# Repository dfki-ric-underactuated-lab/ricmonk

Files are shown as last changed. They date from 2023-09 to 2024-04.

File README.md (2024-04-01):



<div align="center">

# RicMonk: A Three-Link Brachiation Robot with Passive Grippers

</div>

<div align="center">

</div>

## Description
This project offers an open-source and low-cost kit to test control algorithms for underactuated robots. 
It introduces a three-link underactuated brachiation robot called **RicMonk** capable of bidirectional brachiation maneuver with passive grippers inspired from [AcroMonk](https://github.com/dfki-ric-underactuated-lab/acromonk).
RicMonk has two Quasi-Direct-Drives (QDD) that allow dynamic and agile locomotion. 
This project offers different control methods for trajectory stabilization which can be studied using the kit. Additionally, it provides a list of components, discusses best practices for implementation, and presents results from experiments with the simulator and the real system. This repository describes the hardware (CAD, Bill Of Materials ([BOM](/hardware/bills-of-materials.md)), etc.) required to build the physical system and provides the software (URDF models, simulation, and controllers) to control it.

## Research Paper

The work is submitted to the IEEE International Conference on Robotics and Automation (ICRA 2024) and is currently under review. 

## Documentation

The following provides theoretical information regarding the RicMonk:
- [Mechatronic design and integration](/hardware/mechDesAndInt.md)
- [Trajectory optimization](/software/python/simulation/behavior_generation/trajectory_optimization/README.md)
- [Trajectory stabilization](/software/python/simulation/behavior_control/README.md)
- [Bill Of Materials BOM](/hardware/bills-of-materials.md)

For operating the RicMonk, the following may serve as a reference:
- [Basic information](/hardware/README.md)
- [Brachiaiton realization](/software/python/realSystemTests/multipleBrachiationRealize.md)
- [Software Guide](/software/python/README.md)

The CAD file is also provided on grabCAD.com. You can use the 3D viewer from their website to display the 3D model directly within your browser.
 - [Display RicMonk in 3D](https://grabcad.com/library/ricmonk-a-three-link-underactuated-brachiation-robot-with-passive-grippers-1)
## Authors #

* [Shivesh Kumar](https://robotik.dfki-bremen.de/en/about-us/staff/person/shku02) (Team Leader - Mechanics and Control)
* [Mahdi Javadi](https://robotik.dfki-bremen.de/en/about-us/staff/person/maja04) (Project Supervisor, Hardware and Software Concepts, Trajectory Optimization and Stabilization)
* Shourie S. Grama (Hardware and Software Maintainer, Design Optimization, Trajectory Optimization and Stabilization)
* [Hossein Zamani Boroujeni](https://robotik.dfki-bremen.de/en/about-us/staff/person/hoza01) (Tail Design and Gripper Design Improvement. The credit for original arm and gripper design goes to [Daniel Pizzutilo](https://robotik.dfki-bremen.de/de/ueber-uns/mitarbeiter/dapi01) in [AcroMonk](https://github.com/dfki-ric-underactuated-lab/acromonk))

Feel free to contact us if you have questions about the test bench. Enjoy!

## Contributing

1. Fork it (<https://github.com/yourname/yourproject/fork>)
2. Create your feature branch (`git checkout -b feature/fooBar`)
3. Commit your changes (`git commit -am 'Add some fooBar'`)
4. Push to the branch (`git push origin feature/fooBar`)
5. Create a new Pull Request

## Safety Notes #

When working with a real system be careful and mind the following safety measures:

* Brushless motors can be very powerful, moving with tremendous force and speed. Always limit the range of motion, power, force, and speed using configurable parameters, currently limited supplies, and mechanical design.

* The robot must be placed in a ladder bar cage and kept at least one distance from the acromonk in case of operation.

* Make sure you have access to an emergency stop while doing experiments. Be extra careful while operating in the pure torque control loop.

* The robot is equipped with an onboard Lithium Polymer battery and needs proper care and attention. Make sure that you have all the necessary information for the LiPo batteries.

## Acknowledgments #
This work has been supported by the M-RoCK (FKZ01IW21002) and VeryHuman (FKZ01IW20004) projects funded by the German Aerospace Center (DLR) with federal funds from the Federal Ministry of Education and Research (BMBF) and is additionally supported with project funds from the federal state of Bremen for setting up the Underactuated Robotics Lab (201-342-04-2/2021-4-1).

<div align="center">

</div>

## License

This work has been released under the BSD 3-Clause License. Details and terms of use are specified in the LICENSE file within this repository. Note that we do not publish third-party software, hence software packages from other developers are released under their very own terms and conditions, e.g. Stable Baselines (MIT License) and Tensorflow (Apache License v2.0). If you install third-party software packages along with this repo ensure that you follow each license agreement.

## Citation

1. Grama S., Javadi M., Kumar S., Zamani H., Kirchner F., (2024). RicMonk: A Three-Link Brachiation Robot with Passive Grippers for Energy-efficient Brachiation. Submitted in: IEEE International Conference on Robotics and Automation (ICRA).
```
@article{2024_ICRA_ricmonk,
  title={RicMonk: A Three-Link Brachiation Robot with Passive Grippers for Energy-efficient Brachiation},
  author={Grama, Shourie S and Javadi, Mahdi and Kumar, Shivesh and Zamani Boroujeni, Hossein and Kirchner, Frank},
  note={Accepted January 29, 2024 in International Conference on Robotics and Automation (ICRA)}}
```

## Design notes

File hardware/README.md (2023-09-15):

# RicMonk: basic information

Mechatronic design and integration of the RicMonk is addressed [here](../hardware/mechDesAndInt.md). 

## Raspberry Pi and its setup instructions
Raspberry Pi4([setup instructions](https://projects.raspberrypi.org/en/projects/raspberry-pi-setting-up)) is used as a proccessing unit for the RicMonk. Since the Raspberry Pi is housed in the RicMonk, communication to the Raspberry Pi is executed over WiFi using a server computer. An SSH connection is established over WiFi between the server and the Raspberry Pi. To do so, the following steps may be utilized:
- Setup a router
- Connect the Raspberry Pi to a keyboard, a mouse, and a monitor and then power it up
- Connect the Raspberry Pi to the router via WiFi
- Connect the server computer to the router via WiFi
- Get the IP address of the Raspberry Pi using the command `hostname -I` on the Raspberry Pi command line
-Enable SSH/VNC by using `sudo raspi-config` in the Raspberry Pi command line
- Given the username of the Raspberry Pi is `pi` and the IP address is `ipaddress` use the command `ssh pi@ipaddress` the command line of the server

Once all this is set up, there is no requirement to connect the Raspberry Pi to the peripherals anymore. It can be used via SSH.

Information required for pi3hat configuration and commanding motors using tview has been detailed below.

# Moteus tools and Raspberry Pi

Welcome to the documentation for the Pi3hat and Raspberry Pi (RPi) integration. This guide is organized into the following sections:

- Installation
- Sending Commands Using `tview`
- Useful Terminal Commands
- IMU Sensor Data Readings

## Installation

To get started, you'll need to install the necessary dependencies. Follow these steps:

1. Install `moteus` and `moteus_pi3hat` by running the following commands:

```bash
pip3 install moteus
sudo apt install python3-pyside2* python3-serial python3-can python3-matplotlib python3-qtconsole
sudo pip3 install asyncqt importlib_metadata pyelftools
sudo pip3 install --no-deps moteus moteus_gui
sudo pip3 install moteus_pi3hat
```

If you encounter issues related to the `PySide2` dependency, execute these commands:

```bash
pip install PySide2
pip3 install PySide2
sudo apt install python3-pyside2* python3-serial python3-can python3-matplotlib python3-qtconsole
```

Afterward, try installing `moteus_pi3hat` again:

```bash
sudo pip3 install moteus_pi3hat
```

## Sending Commands Using `tview`

Depending on your specific configuration, which includes the bus connected (e.g., CAN) and motor ID, you can use the `tview` tool to connect to your motors. Execute the following command, replacing `BUS` and `MOTOR_ID` with your actual values:

```bash
sudo python3 -m moteus_gui.tview --pi3hat-cfg 'BUS=MOTOR_ID' -t MOTOR_ID
```

For instance, if your CAN connector is attached to `JC3` and the motor ID is `1`, use the following command:

```bash
sudo python3 -m moteus_gui.tview --pi3hat-cfg '3=1' -t 1
```

## Useful Terminal Commands

You can control and manage your motors using terminal commands. To stop or zero-offset a motor, execute these commands, ensuring you adjust the `--pi3hat-cfg` and `-t` options according to your setup. For example, if your CAN connector is connected to `JC3` and the motor ID is `1`, use the following commands:

- Zero-offset the motor:

```bash
sudo moteus_tool --zero-offset --pi3hat-cfg '3=1' -t 1
```

- Stop the motor:

```bash
sudo moteus_tool --stop --pi3hat-cfg '3=1' -t 1
```

### Important Note for Motor and Pi3hat Configuration

Please note that the motor ID for the system is currently set to `7`. Additionally, the only compatible buses with the Pi3hat are `J3` and `J5`. To connect to the motor with the current configuration, use one of the following commands:

```bash
sudo python3 -m moteus_gui.tview --pi3hat-cfg '3=7' -t 7
```

or

```bash
sudo python3 -m moteus_gui.tview --pi3hat-cfg '5=7' -t 7
```

## IMU Sensor Data Readings

### Reading IMU Data from Terminal

To access IMU data, you will need the `pi3hat_tools`. You can download a precompiled version of `pi3hat_tools` by following [this link](https://github.com/mjbots/pi3hat/releases/download/0.1-20210609/20210609-pi3hat_tools-d1e8aa529fe9aa62e6c0df19f10b83bd0e743273.tar.bz2).

**Note:** If your Raspberry Pi does not have an internet connection, you can download the file on your laptop and transfer it to the Raspberry Pi using the steps outlined [here](https://spellfoundry.com/docs/copying-files-to-and-from-raspberry-pi-and-mac/).

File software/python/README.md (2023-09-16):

<div align="center">

# Software guide
</div>

This document provides instruction guides on executions of the software package in simulation and on the Raspberry Pi for real-time execution.

- [Simulation guide](simulation/README.md)
- [RicMonk system guide](realSystemTests/README.md)

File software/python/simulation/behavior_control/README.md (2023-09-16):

# Trajectory Stabilization

Trajectory stabilization is crucial for all robots to ensure trajectory tracking and it has been implemented in RicMonk to help the robot perform brachiation motion. Model-based [Time-varying Linear Quadratic Regulator (TVLQR)](/software/python/simulation/behavior_control/controllers/tvlqr/README.md) and model-free [Proportional-Integral-Derivative (PID) controller](/software/python/simulation/behavior_control/controllers/pid/README.md) that are employed to stabilize the optimal trajectories for the RicMonk.

## Operation
 The file **trajStabilization.py** is to run for stabilizing the trajectories recently optimized, i.e. the trajectories that would be in the folder named after the maneuver in [here](/data/trajectories/direct_collocation/), according to the maneuver. Input the maneuver to be stabilized and also the type of controller to be used (PID or TVLQR). The gains, for either of the controllers have been tuned to enable the controllers to track the trajectories that are stored. The gains may also be modified according to the user's choice by opening the Python file. Running the file would generate the stabilized trajectories. These stabilized trajectories are stored in the folder named concerning the maneuver, controller type, and the date and time of the program run in [here](/data/simulation/). Additionally, the .csv file with the trajectory data and the gains used to stabilize the respective trajectory are also saved in [here](/data/trajectories/closed_loop).

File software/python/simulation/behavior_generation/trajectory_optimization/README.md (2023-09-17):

<div align="center">

# RicMonk Trajectory Optimization
</div>

## Fixed-base model
To optimize trajectories for brachiation, simplify the system, and improve the probability of finding optimal solutions, we use a fixed-base model of the robot as shown in the following figure.

<div align="center">
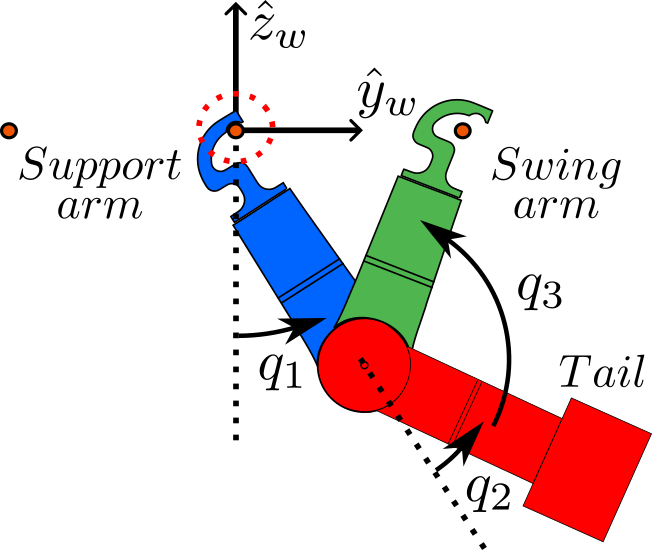
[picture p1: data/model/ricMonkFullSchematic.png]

</div>

In such a model for the RicMonk, the joint between $arm_1$ and ladder bar at $\mathbf{(y_{c}, z_{c})}$ is a revolute joint(dotted circle in the figure). In reality, the arm in contact with the support bar can move if enough force is applied to the arm. Making use of such a model reduces the number of constraints to be imposed, hence simplifying the problem. However, the use of such a fixed-base model has its disadvantages. $arm_1$ cannot let go of the bar, hence trajectories where that happens may not be optimized using this model.

The study on [AcroMonk](https://github.com/dfki-ric-underactuated-lab/acromonk), a two-linked brachiation robot, that is capable of continuously performing robust multiple brachiation maneuvers describes the use of a state machine. The state machine is an implementation that helps the robot to continually brachiate either forward or backward while taking the failure of brachiation into account. For instance, when the robot is not able to successfully catch the bar, when the robot loses all contact with the bar and falls on the ground, when the arm slips off the ladder bar, etc. Given a situation with the robot in any of these cases, the robot either tries to brachiate again using some recovery trajectories or shuts down the actuators to keep the user, the environment, and the robot itself safe. To have such an efficient state machine, the complex brachiation motion was broken down into four distinct simpler maneuvers(a.k.a. atomic behaviors), **ZB**, **ZF**, **BF**, and **FB**. These maneuvers translate respectively to 'zero to back', 'zero to front', 'back to front', and 'front to back'. The forward direction of motion is considered to be the direction in which the hook forms a concave shape. Each of these trajectories is illustrated in the following section. Such an implementation of a state machine enables the robot to perform continuous robust brachiation, even in the face of disturbances. In addition, it simplifies the task of optimizing trajectories. 

Formulation of the trajectory optimization problem is described in [here](formulation.md)

## Gripper Heuristics
Grasp constitutes the action of the robot swing arm hooking onto the surface of the ladder bar, whereas release constitutes the action of the robot swing arm letting go of the ladder bar. Trajectory optimization as [formulated](formulation.md) does not include grasp and release actions, as it does not consider the contact dynamics of the system. As a result, trajectories are optimized from the time instant after the swing arm would have performed the release action to the moment before the swing arm performs the grasp action. These trajectories are called atomic behaviors. Generally, the actions of the swing arm performing release and grasp require the application of a feed-forward torque to the robot's motors. In the case of RicMonk, the weight of the robot and the velocity of the approach of the swing arm toward the target ladder bar take care of the grasp. Hence, for RicMonk to perform the grasp action, no feed-forward torque is applied. However, to perform the release and grasp actions, direct feed-forward torque is applied to the actuators in appropriate directions. The directions and magnitude of the torques were calculated empirically. The following image describes the directions of force applied on the arms due to torque generated in respective motors to enable the robot to perform a release action.

<div align="center">
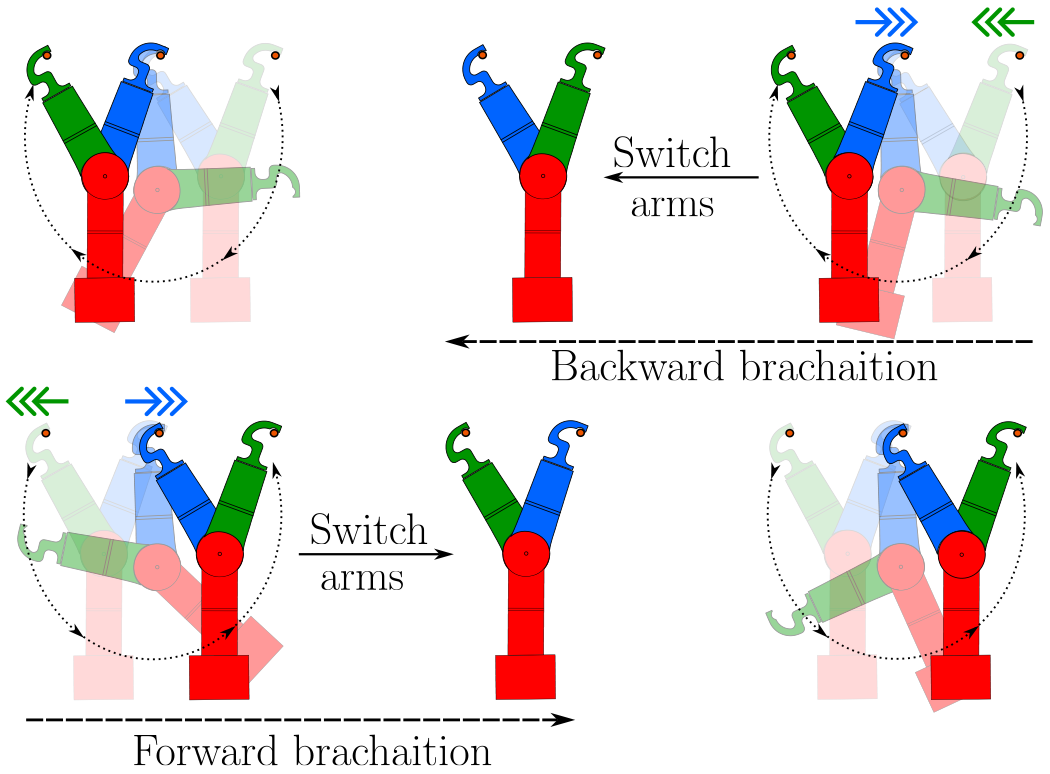
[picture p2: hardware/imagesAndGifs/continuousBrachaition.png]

</div>

To validate the release of the grasp, we monitor the velocity of the swing arm. When the swing arm is still grasping the ladder bar, its velocity remains minimal. We have set a threshold velocity of 1.2 rad/s, which indicates a successful release when the swing arm reaches this velocity. Our tests ensure that only minimal torque is applied to release the grasp from the ladder bar.

## Atomic Behaviors
The swing trajectories for these atomic behaviors are optimized and the animations are obtained as follows. 

<!-- <div align="center">
<img width="500" src="data/model/stateMachine.png" />
</div> -->

<div align="center">
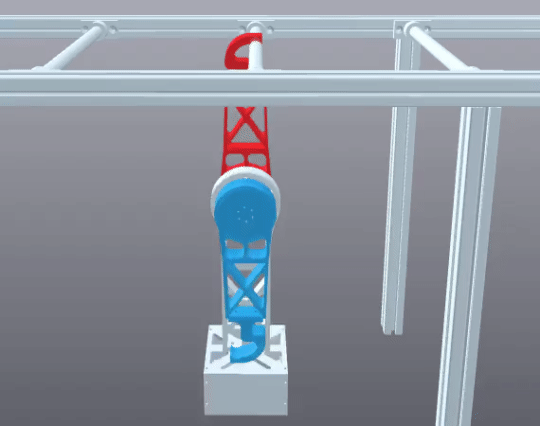
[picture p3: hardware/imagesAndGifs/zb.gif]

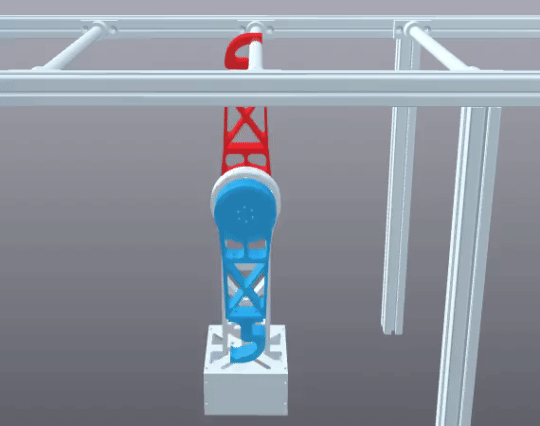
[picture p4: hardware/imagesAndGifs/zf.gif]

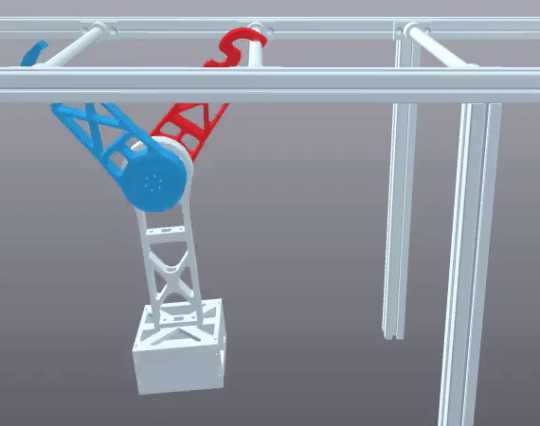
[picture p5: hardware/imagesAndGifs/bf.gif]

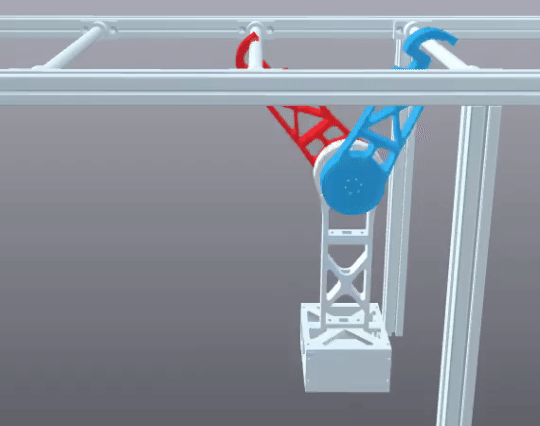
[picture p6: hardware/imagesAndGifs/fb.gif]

</div>

<!---
<div align="center">
<img width="200" src="hardware/imagesAndGifs/ZB_ini_gif.gif" >
<img width="200" src="hardware/imagesAndGifs/ZF_ini_gif.gif" >
<img width="200" src="hardware/imagesAndGifs/BF_ini_gif.gif" >
<img width="200" src="hardware/imagesAndGifs/FB_ini_gif.gif" >
</div>
-->

## Operation
The folder **direct_collocation** contains files that provide the respective hyper-parameters for optimizing trajectories. The file **simulateTrajOpt.py** is to run for optimizing trajectories. Input the name of the trajectory (ZB, ZF, BF, FB) and the ladder bar distance (default = 0.34m). The optimized trajectories are saved in the folder with the name of the maneuver in [here](/data/trajectories/direct_collocation/), according to the maneuver.

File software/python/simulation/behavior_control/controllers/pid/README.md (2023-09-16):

#  Proportional–Integral–Derivative (PID) Control 

## Theory 

The Proportional-Integral-Derivative(PID) controller is a model-free controller, that generates the amount of torque($\mathbf{u}$) supplied by the motors to compensate for the error in the generalized positions($\mathbf{q}$) and velocities($\dot{\mathbf{q}}$) of the robot. The gains $K_p$, $K_i$, and $K_d$ are the proportional, integral, and derivative gains that control the impact of error compensation in generalized positions and velocities respectively. If the desired position and velocity vectors are represented by $\mathbf{q}^*$ and $\dot{\mathbf{q}}^*$, the following equation presents the governing equation of the PID controller.

```math
\begin{equation*}
    \mathbf{u}(t) = K_p \cdot (\mathbf{q}^*(t) - \mathbf{q}(t)) + K_i \cdot \int_{0}^{t} (\mathbf{q}^*(t) - \mathbf{q}(t)) dt + K_d \cdot (\dot{\mathbf{q}}^*(t) - \dot{\mathbf{q}}(t))
\end{equation*}
```

PID controllers are simple to implement. They are efficient in reducing steady errors and they improve system stability. However, the three gains that are required to be manually tuned may pose an error while tuning.  On the other hand, they do not require the model of the system, and their performance is not related to the accuracy of the mathematical model. They may be applied to various systems, and they deliver robust performances.

## Dependencies

The trajectory optimization using direct collocation and PID gains are obtained by taking advantage of [Drake toolbox [2]](https://drake.mit.edu/).

## References

[[1] Russ Tedrake. Underactuated Robotics: Algorithms for Walking, Running, Swimming, Flying, and Manipulation (Course Notes for MIT 6.832).](http://underactuated.mit.edu/)

[[2] Model-Based Design and Verification for Robotics](https://drake.mit.edu/).

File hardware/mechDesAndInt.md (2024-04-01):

<div align="center" >

# Mechatronic Design an Integration
</div>

## Mechanics
Mechanical Design Optimization and integration of necessary electrical components for a functional, capable, and safe operation of a robotic system constitute the Mechatronic integration of the robot. Inspired by the [AcroMonk](https://github.com/dfki-ric-underactuated-lab/acromonk), RicMonk was designed to portable and robust. RicMonk, guided by
the concept of interchangeable and reusable components, stands ready to adapt effortlessly to evolving circumstances. From the bio-inspiration perspective, the RicMonk is closer to Gibbons because of the presence of the tail when compared to the AcroMonk. RicMonk’s tail also plays an important role in the robot’s functioning. It not only provides optimal placement of all the electrical components but also helps extensively in helping the robot brachiate.

<div align="center">
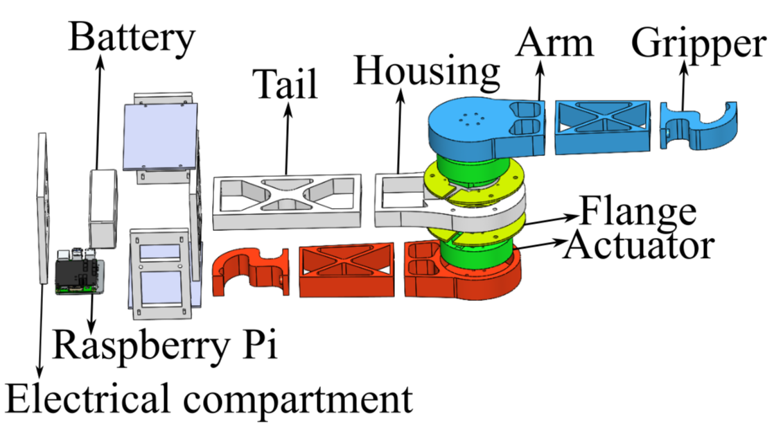
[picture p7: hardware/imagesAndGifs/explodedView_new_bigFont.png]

</div>

<div align="center">
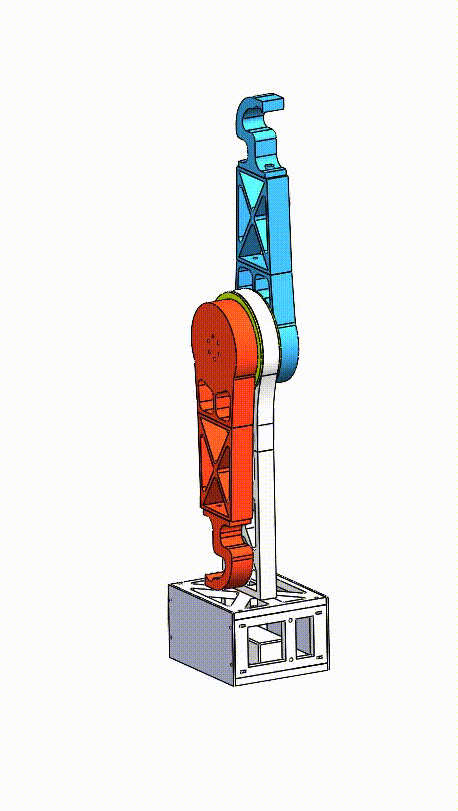
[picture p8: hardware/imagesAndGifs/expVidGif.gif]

</div>

## Electronics
The schematic of the electrical diagram is shown in the following figure.

<div align="center">
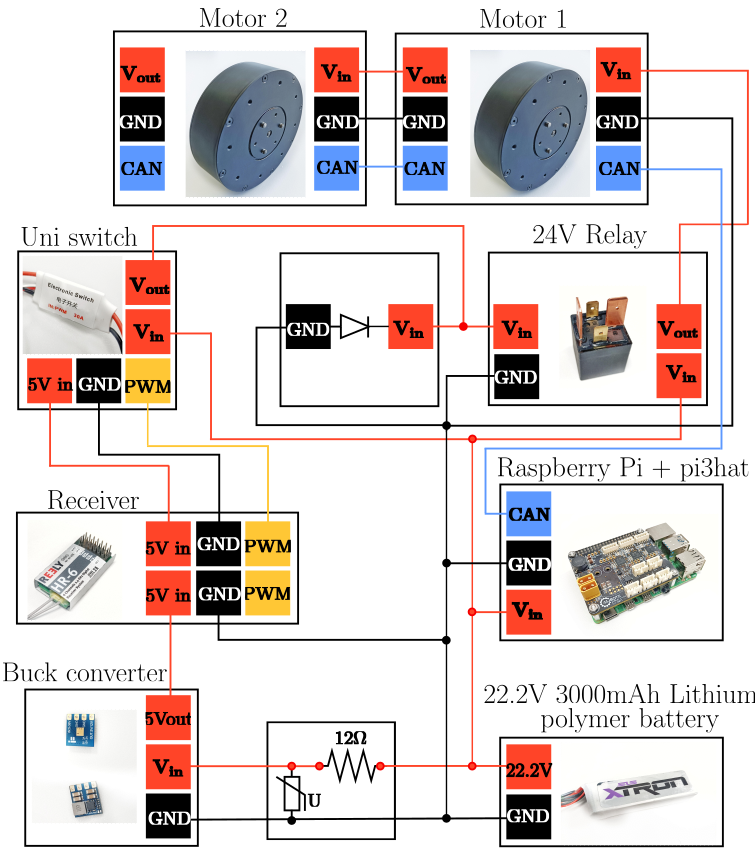
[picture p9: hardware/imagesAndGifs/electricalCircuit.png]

</div>

### Battery
All electronics of the AcroMonk are powered by a LiPo battery with the following technical data:
- Capacity: $6\text{S}\ 3000 \text{ mAh}$ 
- Voltage: $22.2\text{V}$
- Continuous Discharge: max. $30\text{C } (36\text{A})$
- Burst Discharge:max. $60\text{C } (72\text{A})$
- Power: $26.64 \text{ WH}$

### Raspberry Pi and pi3hat
A Raspberry Pi4B ([setup](/hardware/README.md) is used as a processing unit for the robot, and the [mjbots pi3hat](https://mjbots.com/products/mjbots-pi3hat-r4-4b) is used for communication between the Raspberry Pi and the motors. The Inertia Measurement Unit (IMU)([usage](https://github.com/mjbots/pi3hat/blob/master/lib/python/examples/imu_example.py)) on the pi3hat is also used for state estimation purposes. The Raspberry Pi is connected, via WiFi using a Secure Shell Protocol (SSH), to the server that is operated by the user. The Raspberry Pi stores the desired trajectories, the applications to run the robot and help it track trajectories, and measured trajectories.

### Actuator
The actuators used in the RicMonk are the mjbots [qdd100](https://mjbots.com/collections/servos-and-controllers/products/qdd100-beta-3) actuators. These motors are quasi-direct drive motors that provide high torque with sufficient power. These motors also provide the advantages of being back-drivable. 
- [Documentation](https://github.com/mjbots/moteus)
- [Setup](https://www.youtube.com/watch?v=HHCBohdrCH8)

### Emergency Stop
It is necessary to have a safety switch to switch OFF the motors when the robot has an undesired erratic behaviour. To implement the safety switch, a Radio Communication Transmitter Protocol (TX protocol) has been employed to enable a safe operation of the robot. As a result, the electrical circuit includes a transmitter and a receiver. The wiring between the receiver connects to the motors via a 25 A relay, a diode and a 30 A electrical switch. To lower the voltage to the receiver (rated voltage: 6.5 V), a DC-DC converter is used. To avoid the DC-DC converter from getting burnt due to the high frequency voltage fluctuations when the circuit is switched ON, a series combination of a Varistor and a resistor is added to the circuit. This addition dampens the voltage fluctuations in the circuit. As
a result, based on the command from the transmitter, the motors can be directly switched ON and OFF. The electrical switch only controls the functioning of the motors, so the computer (Raspberry Pi) is unaffected by the switching ON and OFF of the motors.

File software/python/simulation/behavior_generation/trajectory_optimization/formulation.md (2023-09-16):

# Trajectory optimization formulation
Taking advantage of the Direct Collocation method by the [Drake](https://drake.mit.edu/) toolbox, and the fixed-base model of the robot, trajectories are optimized for the swing phases using the Sparse Nonlinear OPTimizer([SNOPT](https://www.jstor.org/stable/20453604)). The optimization problem is formulated as follows:

```math
\begin{align*}
    \text{Minimize } \quad & J = W(t_f) + \sum_{n=0}^{N} R(T_1(u_1[n])^2 + T_2(u_2[n])^2) + K(V_1(q_2[n])^2 + V_2(q_3[n])^2) \\
    \text{s.t. } \quad & \text{Dynamics: } \dot{\mathbf{x}}(t_n) = f(\mathbf{x}(t_n), \mathbf{u}(t_n)) \\
    & \text{Costate dynamics: } \dot{\lambda}(t) = -\frac{\partial H}{\partial \mathbf{x}} \\
    & \text{Hamiltonian: } H = L(\mathbf{x}(t_n), \mathbf{u}(t_n)) + \lambda^T f(\mathbf{x}(t_n), \mathbf{u}(t_n)) \\
    & \text{Boundary conditions: } \begin{aligned}[t] 
        \mathbf{x}[0] &= \mathbf{x}_0, \\
        \mathbf{x}[t_f] & \text{ defined using forward geometry and kinematics} \\
        \end{aligned}\\
    & \text{Time step constraint: } 0.005 \leq h[n] \leq 0.5 \\
    & \text{Torque constraints: } |\mathbf{u}[n]| \leq \tau_{\max} \\
    & \text{Velocity constraints: } |\dot{q}_1[n]|, |\dot{q}_2[n]|, |\dot{q}_3[n]| \leq \omega_{\max} \\
    & \text{Position constraints: } |q_1[n]| \leq q_{lim, 1}, |q_2[n]| \leq q_{lim, 2}, |q_3[n]| \leq q_{lim, 3} \\
    & \text{Collision constraints defined using forward geometry}\\
    & \text{Optimization problem warm-started using previously generated trajectories}
\end{align*} 
```
```math
\begin{equation*}
    \mathbf{x} = \begin{bmatrix}
        q_1 \\ q_2 \\ q_3 \\ \dot{q_1} \\ \dot{q_2} \\ \dot{q_3}
    \end{bmatrix} = \begin{bmatrix}
        \mathbf{q} \\ \dot{\mathbf{q}}
    \end{bmatrix}
\end{equation*}
```
```math
\begin{equation*}
    \mathbf{u} = \begin{bmatrix}
        u_1 \\ u_2
    \end{bmatrix}
\end{equation*}   
```

$\mathbf{x}$ and $\mathbf{u}$ are the state vector and the torque vector respectively, and they are the decision variables of the current trajectory optimization problem. $N$ is the number of collocation points that consist of the trajectory. $\mathbf{h}$ is a vector that contains the timesteps that separate the collocation points. $\tau_{max}$ is the imposed motor torque limit and $\omega_{max}$ is the imposed motor angular velocity limit for safe operation of the robot. $q_{lim, 1}$, $q_{lim, 2}$, $q_{lim, 3}$ are the position limits for each of the joint angles. In the cost equation, $R$, $T_1$, and $T_2$ input regularization term and weighting factors for each of the actuators respectively. Also in the same equation, $K$, $V_1$, and $V_2$ are velocity regularization terms and weighting factors for each of the actuators respectively. $W$ is the time penalization constant. The boundary condition for the final time is defined using the forward geometry and kinematics, such that the free end of $arm_2$ catches is at the required position with the required velocity. From the model, we see that the connection of the tail to the arms leads to a kinematic coupling that is not purely serial. Consequently, the inverse kinematics alone cannot directly yield the robot's final state, denoted as $\mathbf{x}(t_f)$, which is a crucial requirement for trajectory optimization.

The output of the following code is not optimal. $\bf{Check}$!

To determine $\mathbf{x}(t_f)$, a methodology is employed involving the desired final spatial position and velocity of the swing arm's gripper, denoted as ${\bf{c}}^*_f$. In each iteration, the solver computes the system's forward kinematics based on the decision variable of the state, represented as $\mathbf{c}_{f}$, and strives to minimize the error relative to $\mathbf{c}_{f}^{*}$. Hence, the final position and velocity of the $tail$ are not explicitly constrained. Collision constraints concerning the free ends of the $tail$ and the $arm_2$ are also defined using the forward geometry of the robot.

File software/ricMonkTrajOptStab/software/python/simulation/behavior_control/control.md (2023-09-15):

# Trajectory Stabilization

Trajectory stabilization is crucial for all robots to ensure trajectory tracking and it has been implemented in RicMonk to help the robot perform brachiation motion. Model-based [Time-varying Linear Quadratic Regulator(TVLQR)](/src/ricMonkTrajOptStab/software/python/simulation/behavior_control/controllers/tvlqr/README.md) and model-free [Proportional-Integral-Derivative(PID) controller](/src/ricMonkTrajOptStab/software/python/simulation/behavior_control/controllers/pid/README.md) that are employed to stabilize the optimal trajectories for the RicMonk.
src="/"
## Operation
 The file **simulateTrajOpt_IPYNB.ipynb** is to run for stabilizing the trajectories recently optimized, i.e. the trajectories that would be in folder named after the maneuver in **../../../../../data/trajectories/direct_collocation/** with respect to the current folder. The **manuever** field may be modified to the choice of trajectory that needs to be optimized. Once done, run the file. The **controller_type** can also be changed to stabilized the trajectory using the PID controller or the TVLQR. The respective gains may be tuned using the variables provided.Running the file would generate the stabilized trajectories. These statbilized trajectories are stored in the folder named with respect to the maneuver, controller type and the date and time of program run. This folder is saved within the **../../../../../results** with respect to the current folder. Additionally, the .csv file with the trajectory data and the gains used to stabilize the respective trajectory are also saved in **../../../../../data/trajectories/closed_loop** with respect to the current folder.

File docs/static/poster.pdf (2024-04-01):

RicMonk: A Three-Link Brachiation Robot with Passive Grippers for Energy-Efficient Brachiation

Abstract
Brachiation (illustrated in Fig. 1), a mode common among primates like long-armed gibbons, involves swinging between tree branches using only their arms. This locomotion mode holds potential for diverse applications such as agriculture surveillance, forest exploration, and biomimetic design. This paper presents the design, analysis, and performance evaluation of RicMonk, a novel three-link brachiation robot equipped with passive hook-shaped grippers. The paper discusses the use of the Direct Collocation methodology for optimizing trajectories for the robot’s dynamic behaviors and stabilization of these trajectories using a Time-varying Linear Quadratic Regulator. With RicMonk we demonstrate bidirectional brachiation, and provide comparative analysis with its predecessor, AcroMonk [1]- a two-link brachiation robot, to demonstrate that the presence of a passive tail helps improve energy efficiency.

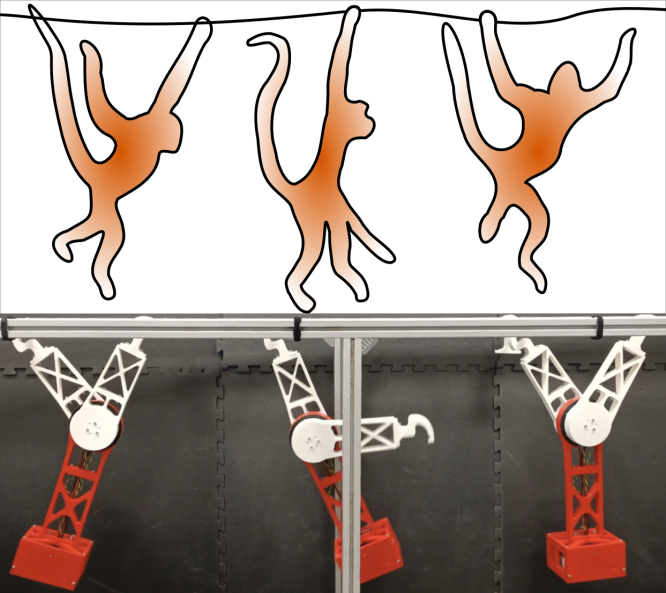
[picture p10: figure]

Figure: Brachiation illustration

Open-source code

The system design, controllers, and software implementation are publicly available on GitHub and the video demonstration of the experiments can be viewed on Youtube. Scan the following QR code to access the GitHub page where the link to the Youtube video is also available.

Mechatronics Design

As envisioned in the preceding generation of the RicMonk, the AcroMonk [1], the design should be compact, and wireless and needs to be made of readily available and lowcost materials. The arms and passive gripper are inspired by AcroMonk. RicMonk is equipped with two actuators and a tail that mimics a monkey’s body, as depicted in Fig. 2. Electrical components and the battery reside securely in the tail’s bottom box. A stable gripper design is critical during swinging. The original cylindrical pivot lacked stability due to an offset center of mass, causing sway and weak contact. This instability led to undesired motion with one arm on the ladder bar. To solve this, a conical pivotal surface was introduced, accommodating the offset. This improved stability, although a tight grip required higher release torque. Also, this gripper design results in mirroring symmetry rather than full sagittal symmetry in RicMonk.

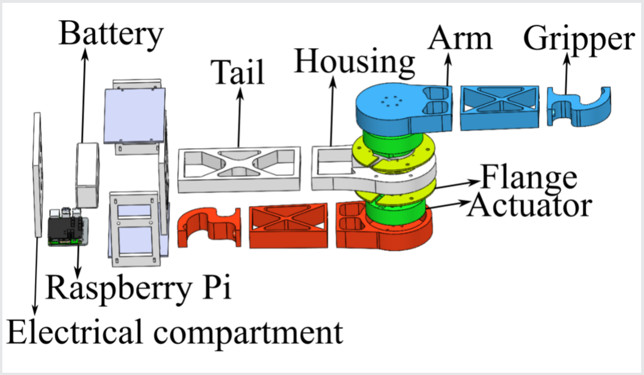
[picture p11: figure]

Figure: RicMonk exploded view

Trajectory Optimization

Brachiation is divided into four simple atomic behaviours -ZB (Zero - Back bar), ZF (Zero - Front bar), BF (Back bar
- Front bar), FB (Front bar - Back bar); as defined in [1]. These trajectories (state variables and inputs) are optimized, for a fixed base model of RicMonk (Fig. 3, dotted red circle represents a revolute joint), using the Direct Collocation method, by minimizing a cost dependent on the energy expended during the respective maneuver.

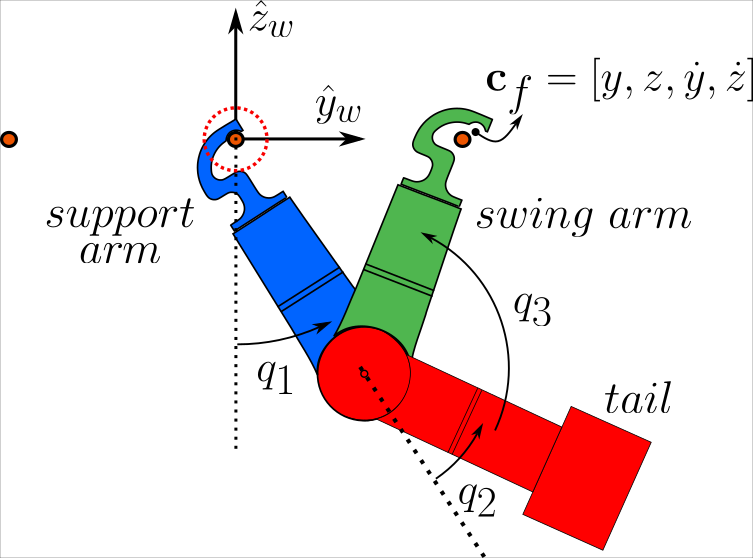
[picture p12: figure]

Figure: RicMonk fixed base model

Trajectory Stabilization

Each of the trajectories is stabilized using the Time-varying Linear Quadratic-Regulator (TVLQR) in simulation and reality. With the real system, TVLQR is used as an offline controller and the pre-computed optimal time-varying feedback matrix is used for online error compensation on a control loop running at approximately 400 Hz.

Experimental Validation

Atomic behaviors were executed on the real system using the TVLQR controller. State estimation accommodating the RicMonk arm’s complete revolution enabled combining atomic behaviors, facilitating continuous brachiation. Fig. 4 and 5 illustrate RicMonk performing multiple forward and backward directions respectively. The controller is robust against soft disturbances in the path of the robot, and excess weight. Fig. 6 displays variation in robot’s position during recovery from disturbance during brachiation.

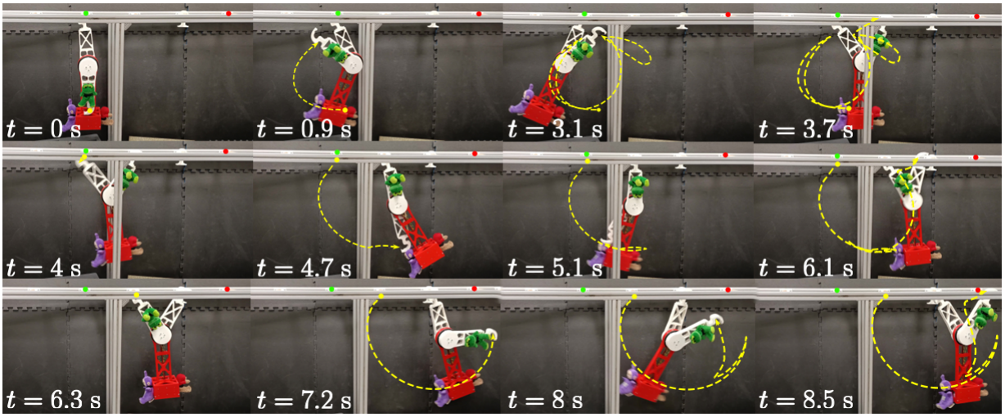
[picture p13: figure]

Figure: RicMonk performing multiple forward brachiation cycles. Row one - ZF maneuver (left to right), row two and three - BF maneuvers (left to right)

Comparative analysis

Cost of Transport (CoT) [2] is a dimensionless measure for energy efficiency, allowing comparison across sizes and structures. Formulated as Eq. 1, it factors in energy input (E), mass (m), distance (d), and gravity acceleration (g).

CoT =

E
mgd

(1)

The lower the CoT value, the more energy-efficient a given system is. Table 1 compares total energy consumed (TE), CoT, and time taken(t) during five continuous forward brachiation maneuvers for AcroMonk and RicMonk. RicMonk, with the tail, is more energy efficient compared to AcroMonk. However, AcroMonk consumes a lower amount of energy in total.

Table: Comparitive analysis
TE (J) CoT t (s)
AcroMonk 8.9547 0.3355 11
RicMonk 15.1947 0.2760 17

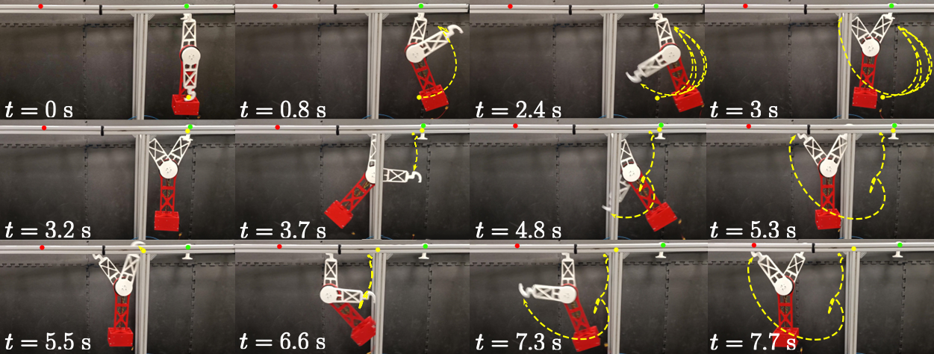
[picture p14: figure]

Figure: RicMonk performing multiple backward brachiation cycles. Row one - ZB maneuver (left to right), row two and three - FB maneuvers (left to right)

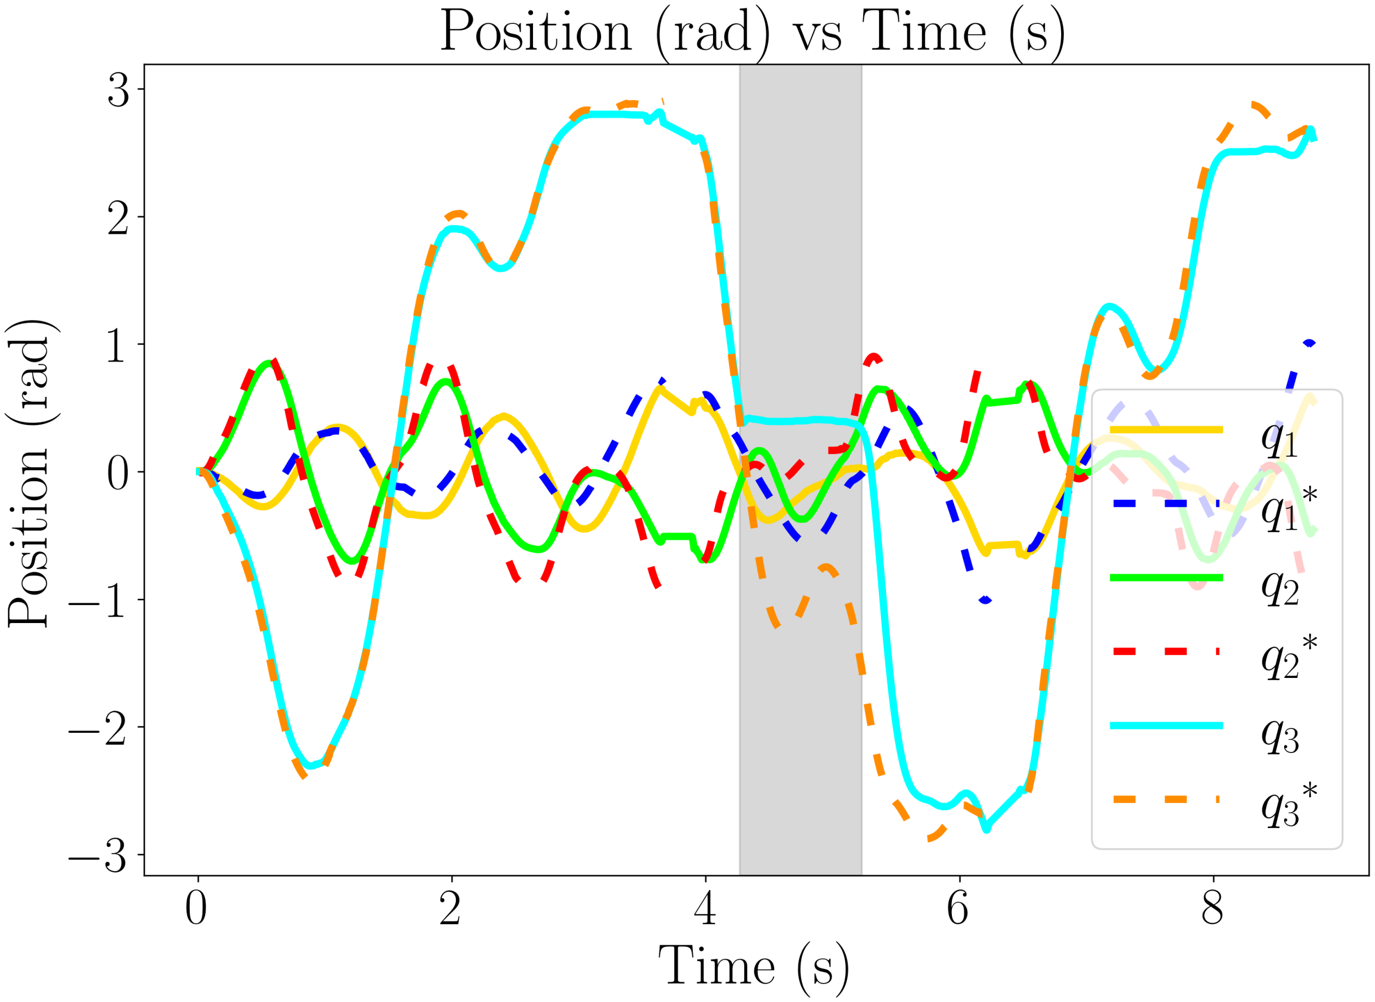
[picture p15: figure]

Figure: Position plot of RicMonk performing multiple brachiation in face of disturbances in its path. Shaded region of the plots signify disturbance in robot motion

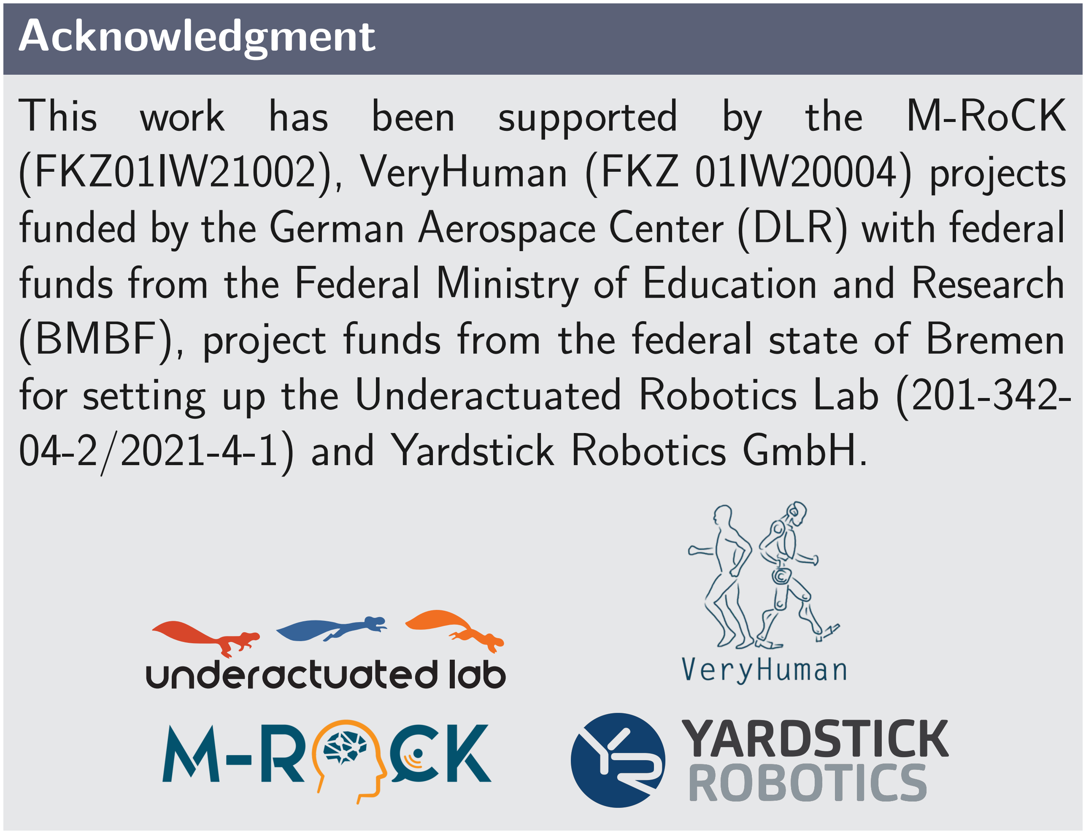
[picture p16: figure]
Acknowledgment; (FKZ01IW21002), VeryHuman (FKZ 01IW20004) projects; 04-2/2021-4-1) and Yardstick Robotics GmbH.

This work has been supported by the M-RoCK

funded by the German Aerospace Center (DLR) with federal funds from the Federal Ministry of Education and Research (BMBF), project funds from the federal state of Bremen for setting up the Underactuated Robotics Lab (201-342-

References

[1] Mahdi Javadi et al. “AcroMonk: A Minimalist Underactuated Brachiating Robot”. In: IEEE Robotics and Automation Letters (2023).
[2] Sangbae Kim, Patrick M Wensing, et al. “Design of dynamic legged robots”. In: Foundations and Trends® in Robotics 5.2 (2017), pp. 117–190.
Submission #1204 | shouriegs00.sgs@gmail.com, mahdi.javadi@dfki.de ,
1 Yardstick Robotics GmBH, Germany.

2 DFKI RIC GmbH, Germany.

3 University of Bremen, Germany.

4 Chalmers University of Technology, Sweden.

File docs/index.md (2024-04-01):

---
title: "RicMonk: A Three-Link Brachiation Robot with Passive Grippers for Energy-Efficient Brachiation"
pdf: https://arxiv.org/abs/2403.15762
youtube: https://youtu.be/hOuDQI7CD8w?si=d_ABz1Ux-a2fxKTy
github: https://github.com/dfki-ric-underactuated-lab/ricmonk
poster: static/poster.pdf
authors:
  - {name: Shourie S.  Grama, affiliation_key: 1, link: https://www.shouriegs.com/}
  - {name: Mahdi Javadi, affiliation_key: 1, link: https://robotik.dfki-bremen.de/de/ueber-uns/mitarbeiter/maja04.html}
  - {name: Shivesh Kumar, affiliation_key: [3,1], link: https://robotik.dfki-bremen.de/de/ueber-uns/mitarbeiter/shku02.html}  
  - {name: Hossein Zamani Boroujeni, affiliation_key: 1, link: https://robotik.dfki-bremen.de/de/ueber-uns/mitarbeiter/hoza01.html}
  - {name: Frank Kirchner, affiliation_key: [2,1], link: https://robotik.dfki-bremen.de/de/ueber-uns/mitarbeiter/frki01.html}
affiliations:
  - {name: German Research Center for Artificial Intelligence, affiliation_key: 1, link: https://robotik.dfki-bremen.de/de/startseite}
  - {name: Universität Bremen, affiliation_key: 2, link: https://www.uni-bremen.de/robotik}
  - {name: Chalmers University of Technology, affiliation_key: 3, link: https://www.chalmers.se/en/}

---

## Introduction
This paper presents the design, analysis, and performance evaluation of RicMonk, a novel three-link brachiation robot equipped with passive hook-shaped grippers. 
Brachiation, an agile and energy-efficient mode of locomotion observed in primates, has inspired the development of RicMonk to explore versatile locomotion and maneuvers on ladder-like structures. 
The robot's anatomical resemblance to gibbons and the integration of a tail mechanism for energy injection contribute to its unique capabilities. 
The paper discusses the use of the Direct Collocation methodology for optimizing trajectories for the robot's dynamic behaviors and stabilization of these trajectories using a Time-varying Linear Quadratic Regulator. 
With RicMonk we demonstrate bidirectional brachiation, and provide comparative analysis with its predecessor, [AcroMonk](https://github.com/dfki-ric-underactuated-lab/acromonk) - a two-link brachiation robot, to demonstrate that the presence of a passive tail helps improve energy efficiency. 
The system design, controllers, and software implementation are publicly available on [GitHub](https://github.com/dfki-ric-underactuated-lab/ricmonk).

## Experimental Results
Javadi *et al.* in [AcroMonk](https://arxiv.org/abs/2305.08373) proposed a state machine to ensure robust and continuous forward or backward brachiation while accounting for potential failures.  RicMonk also employs a similar state machine that integrates *gripper-related heuristics* with a swing phase to generate a maneuver. The swing motion is associated with a sequence of transitions among three fixed configurations, referred to as [*atomic behaviors*](https://github.com/dfki-ric-underactuated-lab/ricmonk/blob/main/software/python/simulation/behavior_generation/trajectory_optimization/README.md).

All the atomic behaviors are [tested with RicMonk](https://youtu.be/hOuDQI7CD8w?t=20) and only continuous backward brachiation is presented here for brevity. 

<figure>
  
  <figcaption>Fig.1 - RicMonk performing continuous backward brachiation</figcaption>
</figure>

## Results and Discussion

<table>
  <tbody>
    <tr align="center" valign="center">
      <td>
        <figure>
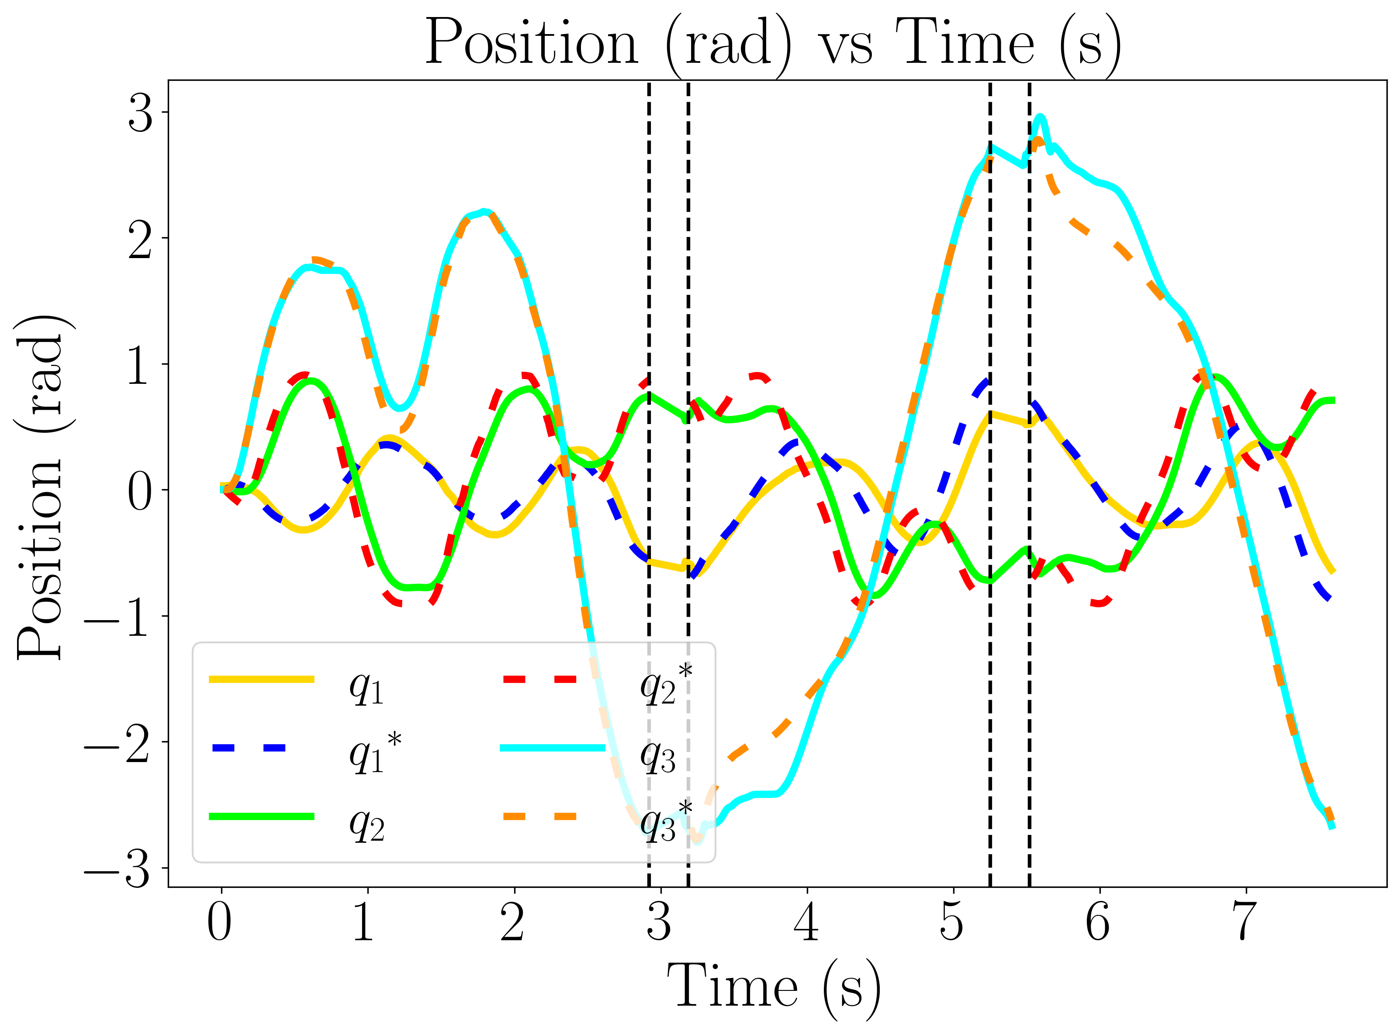
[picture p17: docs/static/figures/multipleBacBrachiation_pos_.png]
          
          <figcaption>Fig.2 - Position plot for backward brachiation</figcaption>
        <figure>
      </td>
      <td>
        </figure>
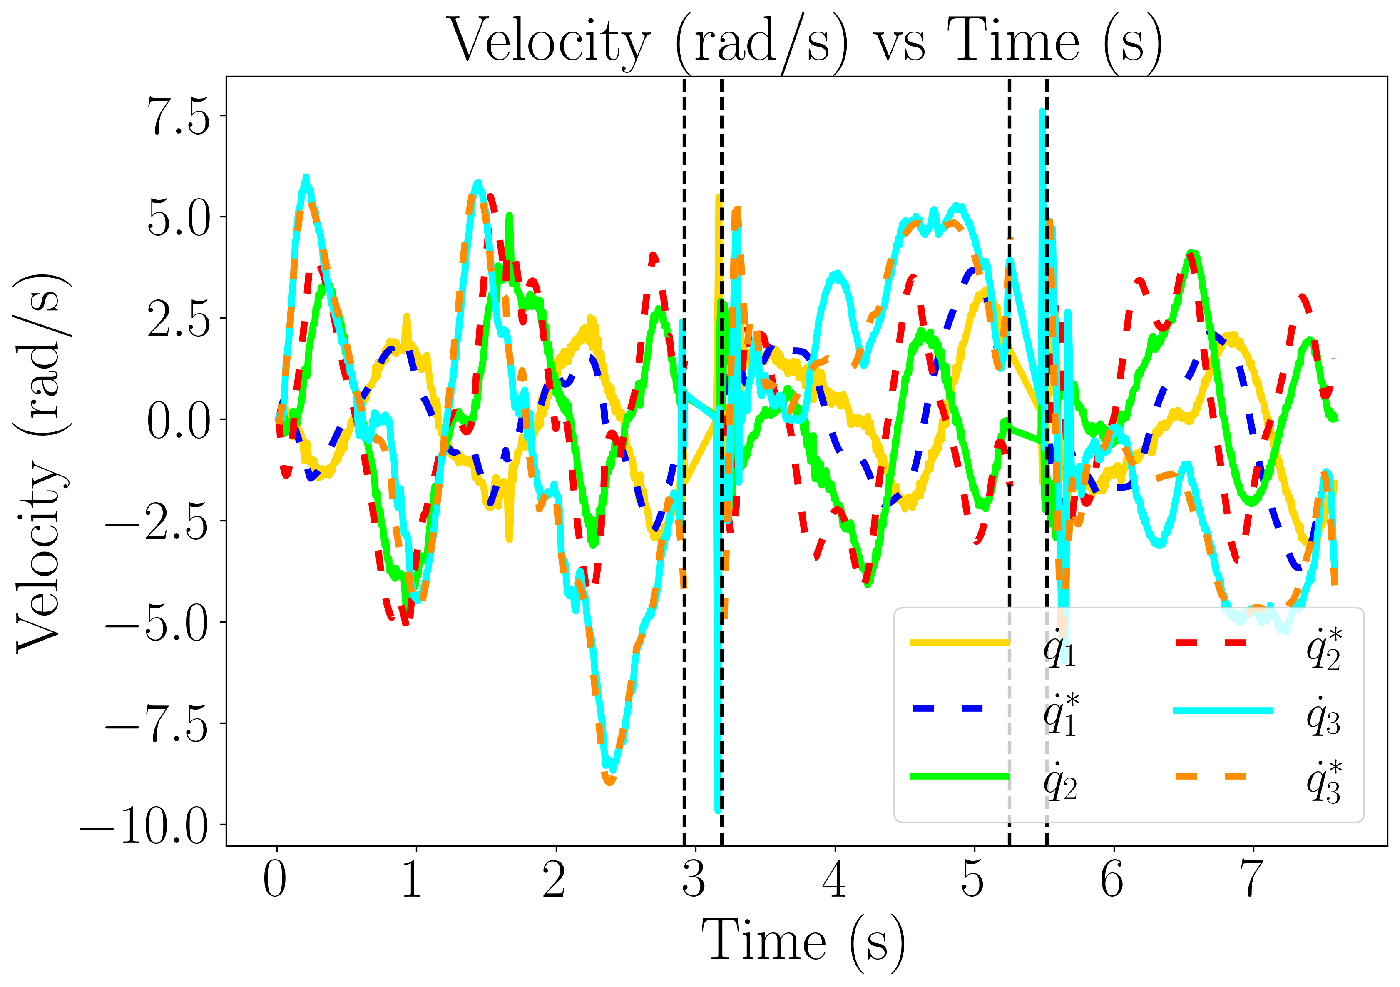
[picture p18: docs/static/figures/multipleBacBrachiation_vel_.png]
          
          <figcaption>Fig.3 - Velocity plot for backward brachiation</figcaption>
        </figure>
      </td>
    </tr>
    <tr align="center" valign="center">
      <td>
        <figure>
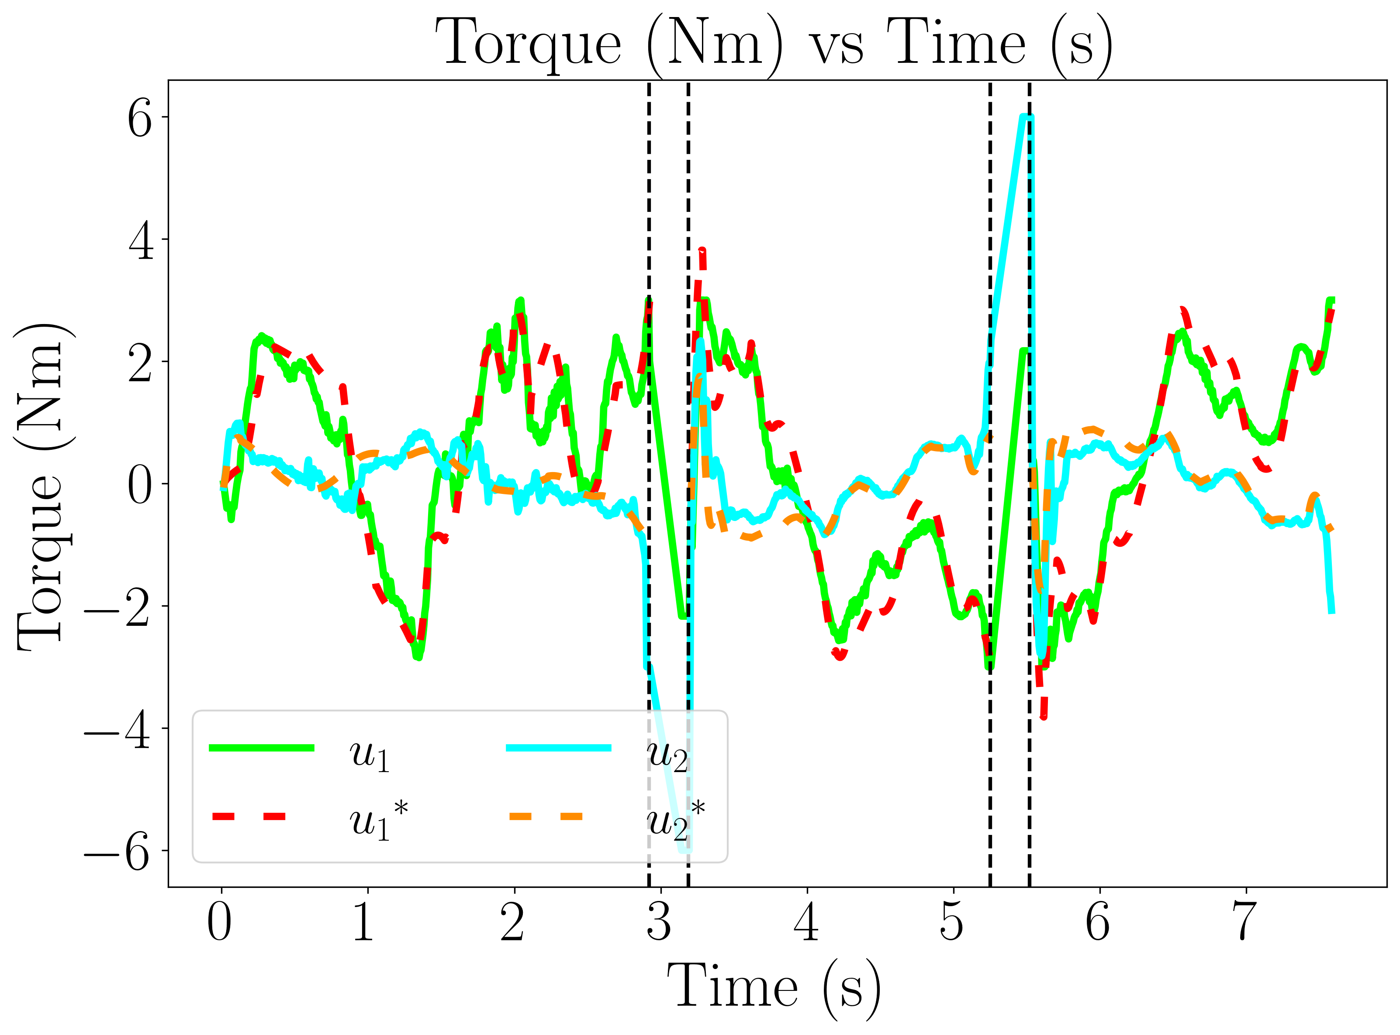
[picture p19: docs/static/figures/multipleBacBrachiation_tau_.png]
          
          <figcaption>Fig.4 - Torque plot for backward brachiation</figcaption>
        </figure>
      </td>
      <td>
        <figure>
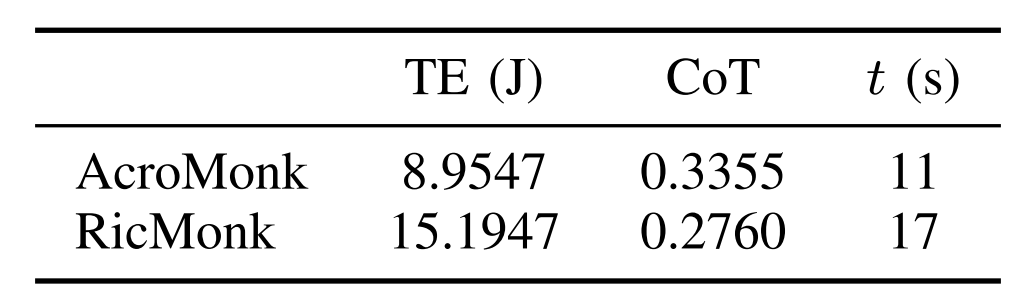
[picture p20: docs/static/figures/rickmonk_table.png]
          
          <figcaption>Table.1 - Comparitive analysis</figcaption>
        </figure>
      </td>
    </tr>
  </tbody>
</table>

Fig.2-4 illusterates presents experimental results of RicMonk performing three consecutive backward brachiation maneuvers (the desired indicated with superscript * and measured positions, velocities, and input torques with solid lines). The plots demonstrate reasonable tracking of desired trajectories resulting in successful brachiation.  

A comparitive analysis is done for AcroMonk and RicMonk and the results are presented in Table.1. Cost of Transport (CoT) is a dimensionless measure for energy efficiency, allowing comparison across sizes and structures. The table highlights several key insights. Though AcroMonk consumes a lot less energy in total, RicMonk has a lower CoT, indicating higher energy efficiency.

The controller's robustness in executing multiple brachiation maneuvers is investigated through several tests, including extra weight, disturbance rejection. In all the scenarios, the controller effectively stabilized the trajectories, enabling RicMonk to perform multiple brachiation maneuvers in two out of three trials. 

<table>
<figure>
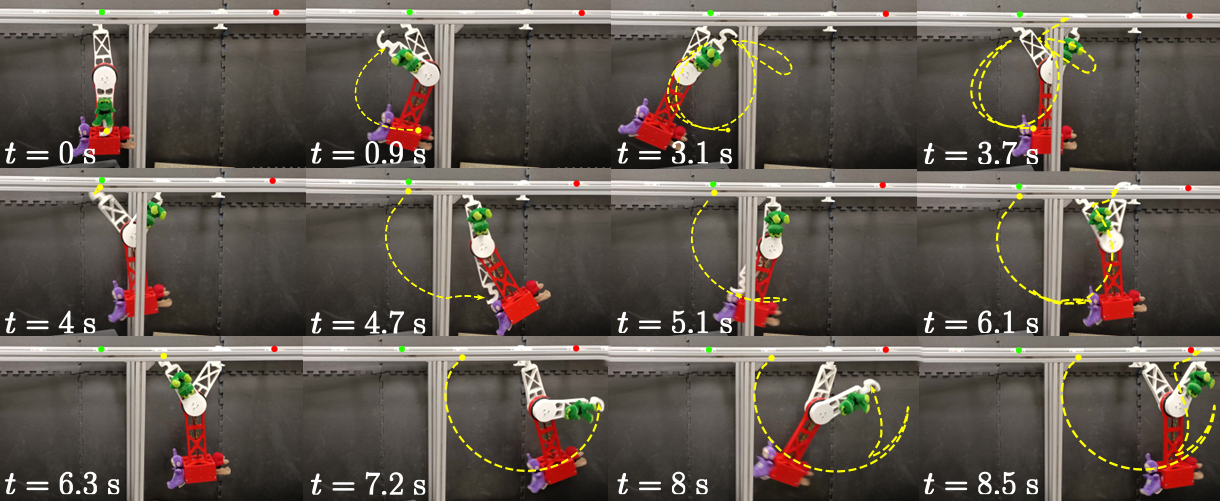
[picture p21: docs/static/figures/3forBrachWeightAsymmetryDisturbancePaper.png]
  
  <figcaption>Fig.5 - Snapshots of RicMonk performing multiple brachiation motions in the presence of mass uncertainty that is loaded
asymmetrically</figcaption>
<figure>
</table>

<p>
To summarise the work,
<ul>
<li> This paper addressed the mechatronic design, generation, and stabilization of optimal trajectories, and experimental validation of RicMonk, a three-link underactuated brachiation robot, with passive grippers.</li>
<li>  The presence of a tail structure and two actuators help RicMonk to perform multiple brachiation maneuvers in both forward and backward directions and this is a novelty in literature. The presence of the tail also improves the energy efficiency as shown by the comparison of cost of transport</li>
<li> System design and controllers are open-sourced and available online. 
</li>
</ul>
</p>

## Citation
```
@article{2024_ICRA_ricmonk,
  title={RicMonk: A Three-Link Brachiation Robot with Passive Grippers for Energy-efficient Brachiation},
  author={Grama, Shourie S and Javadi, Mahdi and Kumar, Shivesh and Zamani Boroujeni, Hossein and Kirchner, Frank},
  note={Accepted January 29, 2024 in International Conference on Robotics and Automation (ICRA)}}
```

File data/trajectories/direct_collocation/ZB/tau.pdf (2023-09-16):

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

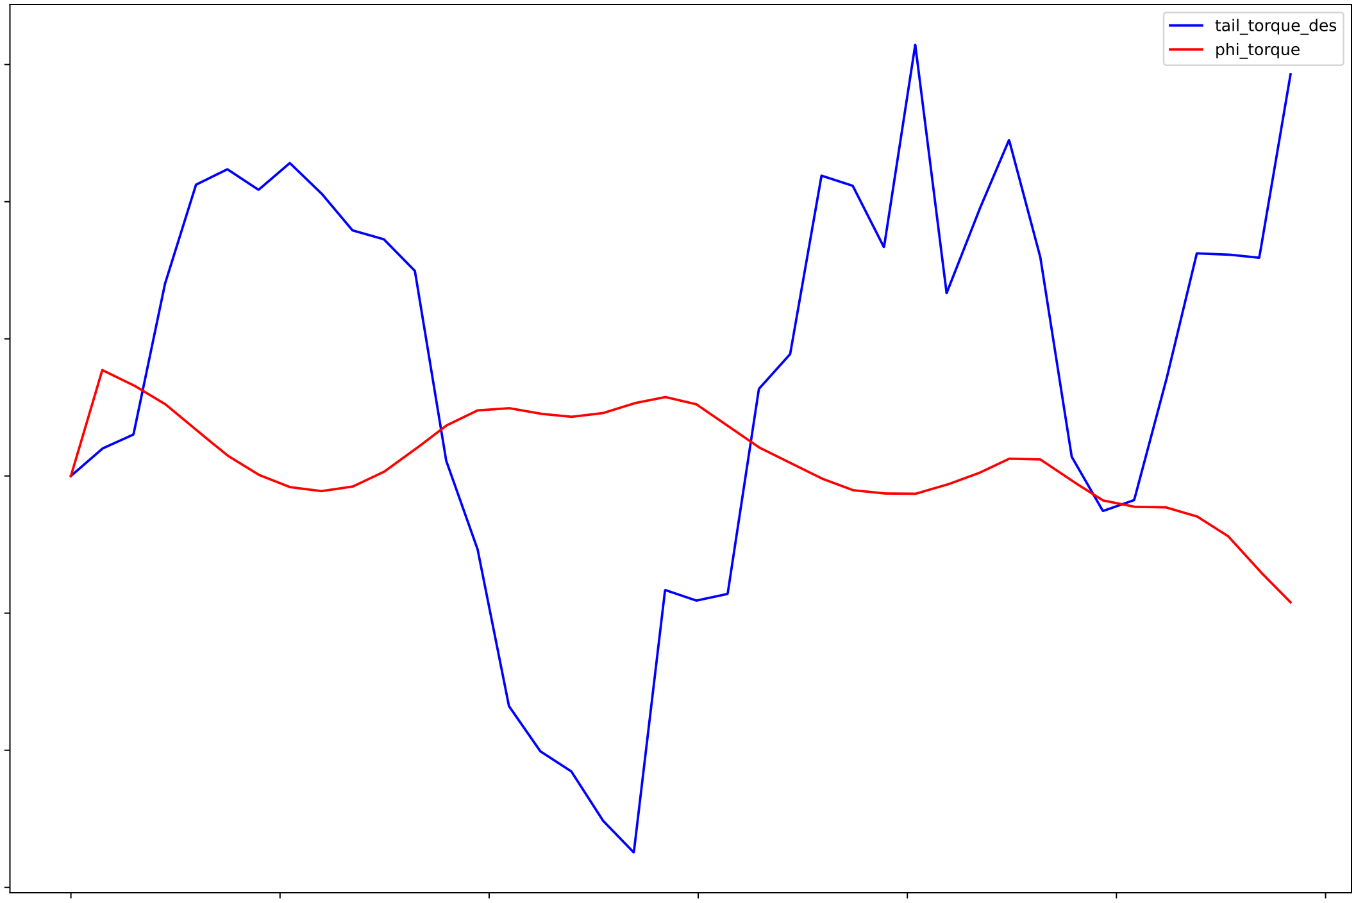
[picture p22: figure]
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

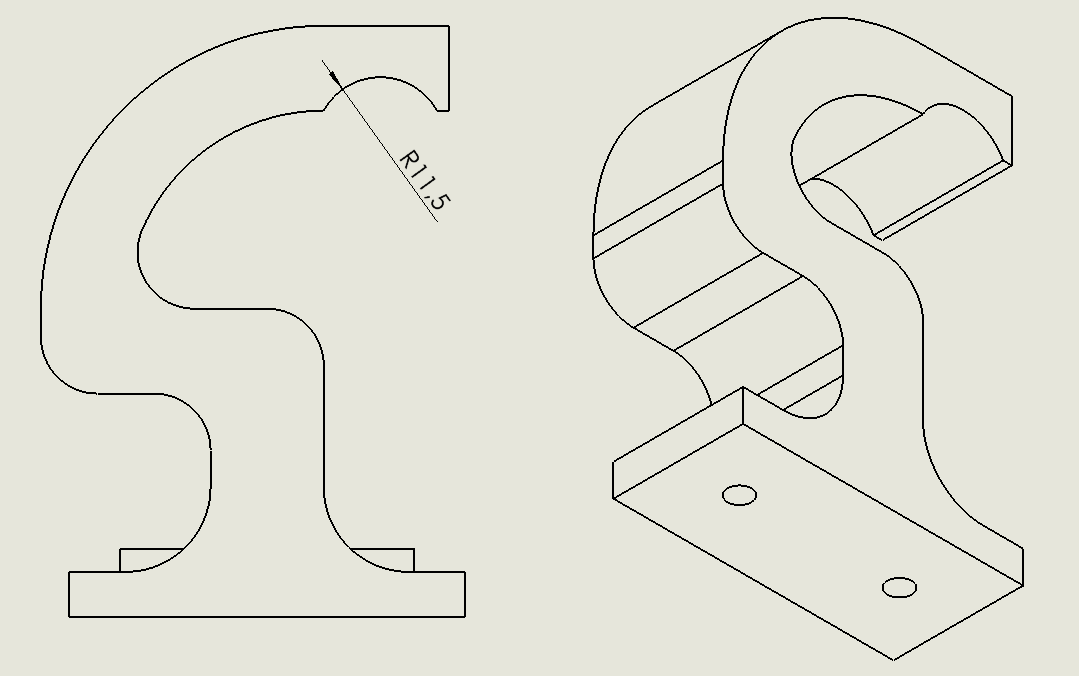
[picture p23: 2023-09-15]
hardware/imagesAndGifs/hook_even.png

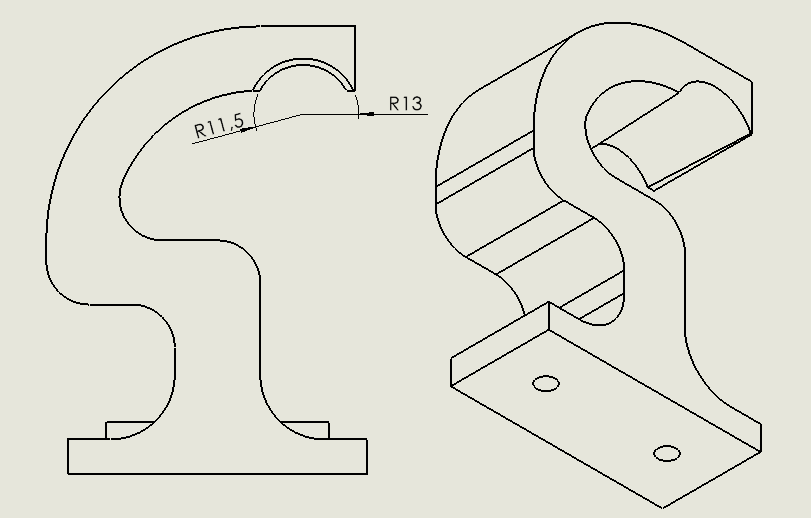
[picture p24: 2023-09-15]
hardware/imagesAndGifs/hook_conic.png

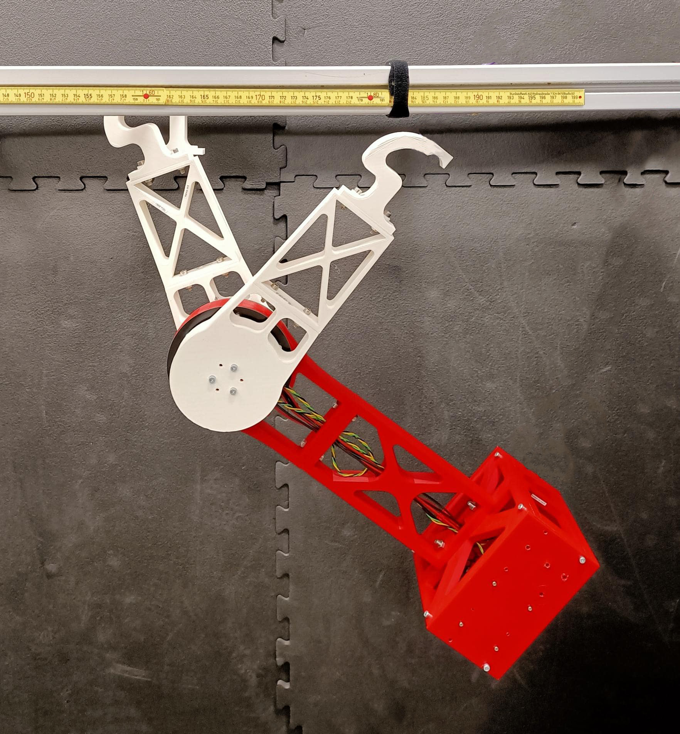
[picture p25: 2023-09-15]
hardware/imagesAndGifs/RicMonk.jpg

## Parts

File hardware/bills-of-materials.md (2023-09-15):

<div align="center">

# Bill of Materials
</div>
This document provides the bill of materials that is used for the AcroMonk testbench. 

|Material|Price in Germany (Euro)|Sample Provider|
|:--|:--:|:--:|
|LiPo Battery|65|[purchase link](https://www.stefansliposhop.de/akkus/sls-xtron/sls-xtron-30c/sls-xtron-3000mah-6s1p-22-2v-30c-60c::1034.html)|
|Raspberry Pi 4 Modell B 4 GB|70|[purchase link](https://www.rasppishop.de/Raspberry-Pi-4-Modell-B-4GB-SDRAM)|
|MicroSD 64GB|12|[purchase link](https://www.rasppishop.de/Sandisk-microSDHC-UHS-I-64GB-Class10-mit-Raspberry-Pi-OS)|
|Two qdd100 beta 3 servos|1078.00 \$|[purchase link](https://mjbots.com/collections/servos-and-controllers/products/qdd100-beta-3)|
|mjbots pi3hat|149.00 \$|[purchase link](https://mjbots.com/products/mjbots-pi3hat-r4-4b)|\
|Reely joystick|74|[purchase link](https://www.conrad.de/de/p/reely-ht-6-hand-fernsteuerung-2-4-ghz-anzahl-kanaele-6-inkl-empfaenger-1310037.html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)|
|Step-Down Voltage Regulator|5|[purchase link](https://www.fpv24.com/en/iflight/iflight-5v12v-step-down-voltage-regulator-2-8s-micro-bec)|
|24V DC Relay|10|[purchase link](https://www.conrad.com/p/zettler-electronics-az979-1c-24d-automotive-relay-24-v-dc-60-a-1-change-over-507417)|
|Electonic switch 30A|20|[purchase link](https://www.amazon.de/Dilwe-Elektrischer-Schalter-Fernbedienung-Ersatzteil/dp/B07R1VGSNN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)|
|BASF Ultrafuse PLA|54|[purchase link](https://www.conrad.de/de/p/basf-ultrafuse-pla-0002a075-pla-black-filament-pla-1-75-mm-750-g-schwarz-1-st-1417247.html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)|
|Screws, nuts, bolts|10|--|
|Resistor, varistor and cables|10|--|
|3D printing cost|--|--|
|Total estimated cost|1400-1700|

## Notes
* The underactuated lab does not have any relation with the providers and does not accept any responsibility for any possible issues with the third parties. 
* The shipping and 3D printing expenses are excluded from the total cost.

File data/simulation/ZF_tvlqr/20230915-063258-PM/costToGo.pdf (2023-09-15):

### Cost-to-go TVLQR (Nm) vs Time (s)

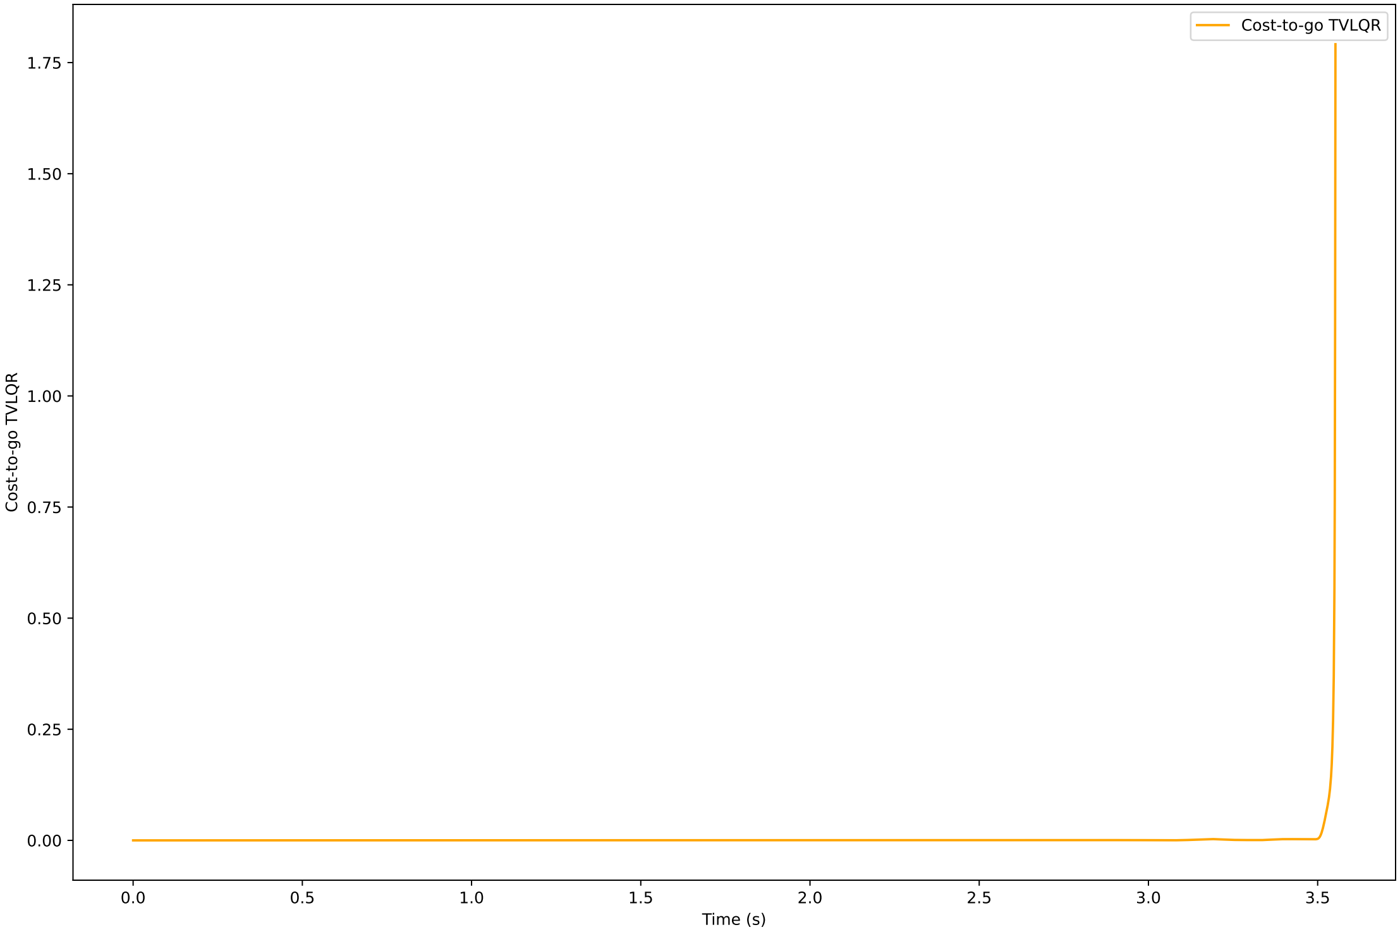
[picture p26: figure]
Time (s); Cost-to-go TVLQR

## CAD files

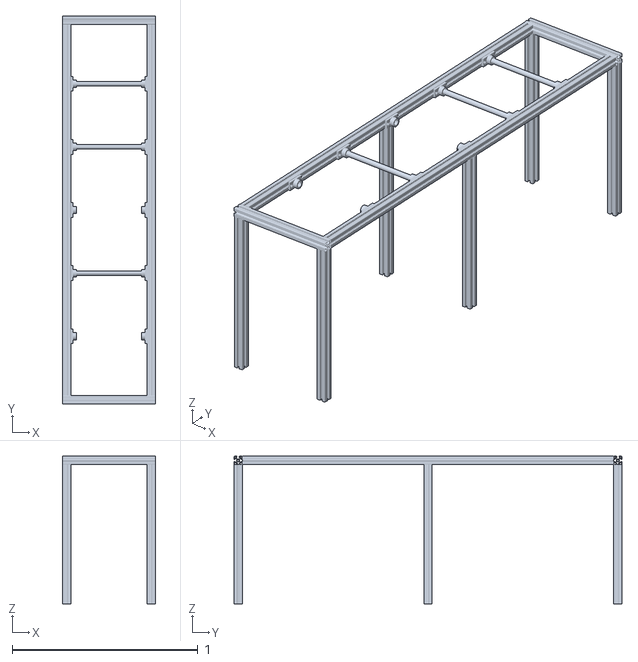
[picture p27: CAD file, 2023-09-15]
data/simulation_models/meshes/Base.STL
0.5 x 2.09 x 0.795

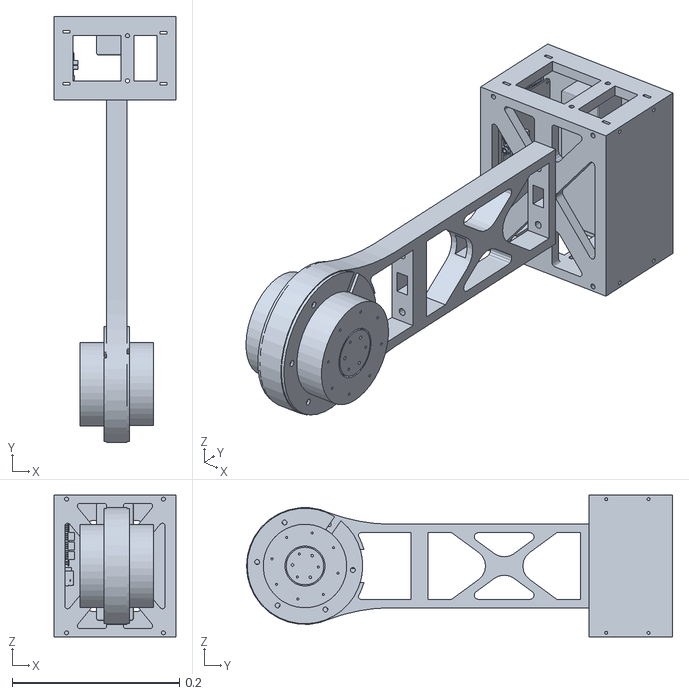
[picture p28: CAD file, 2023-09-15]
data/simulation_models/meshes/tail.STL
0.146 x 0.51 x 0.17

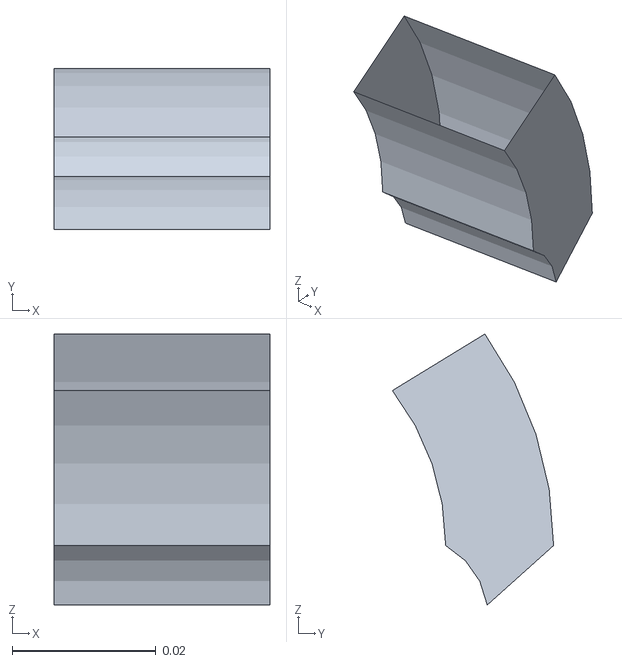
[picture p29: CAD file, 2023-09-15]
data/simulation_models/meshes/hook_2_upper_lower.STL
0.03 x 0.0224 x 0.0377

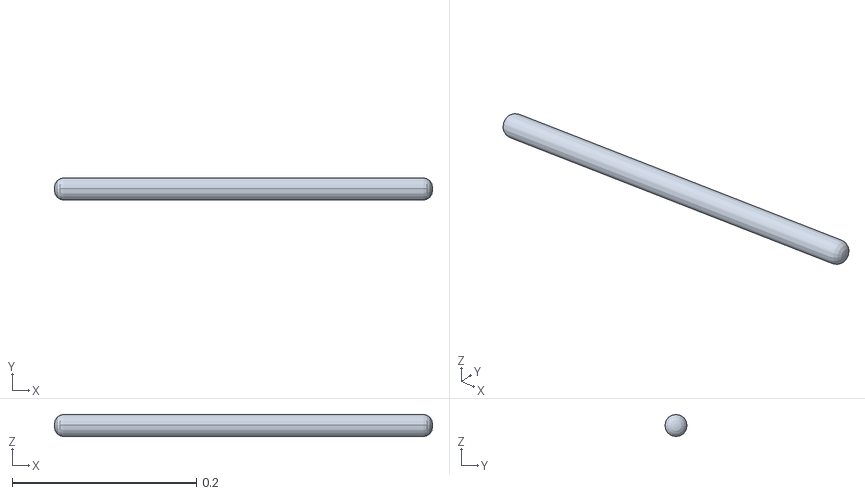
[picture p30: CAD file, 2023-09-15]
data/simulation_models/meshes/stick_1.STL
0.41 x 0.024 x 0.024

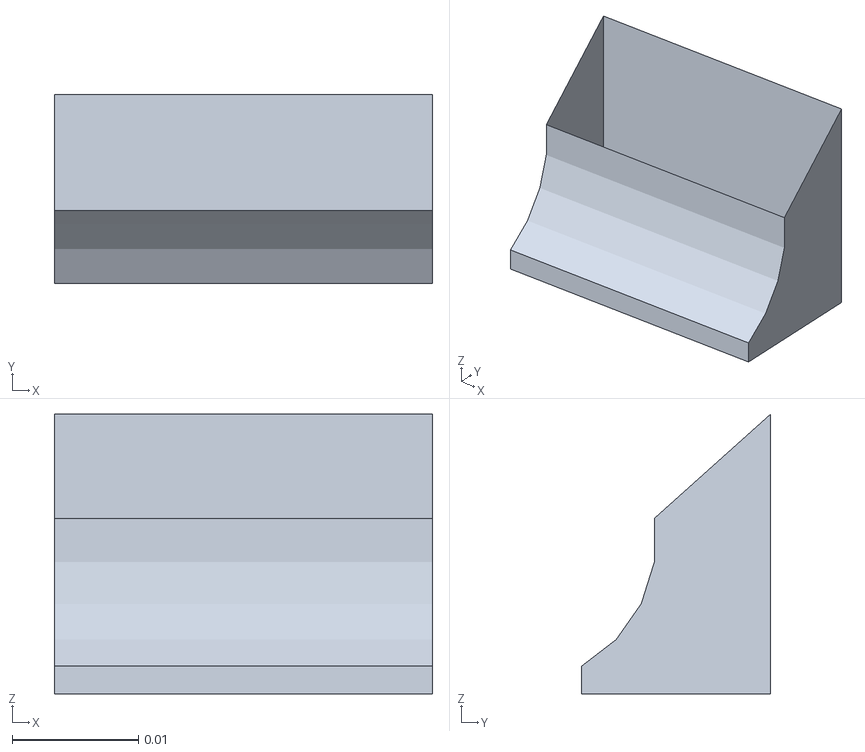
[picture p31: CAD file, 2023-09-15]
data/simulation_models/meshes/hook_2_upper_tip.STL
0.03 x 0.015 x 0.0222

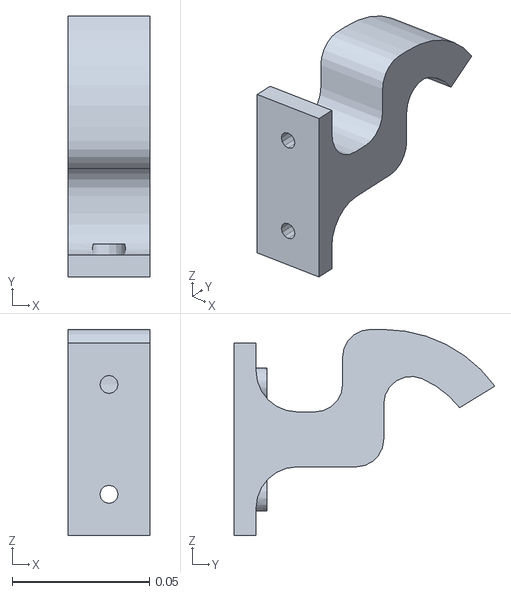
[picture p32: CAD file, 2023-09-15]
data/simulation_models/meshes/hook_2_lower.STL
0.03 x 0.095 x 0.075

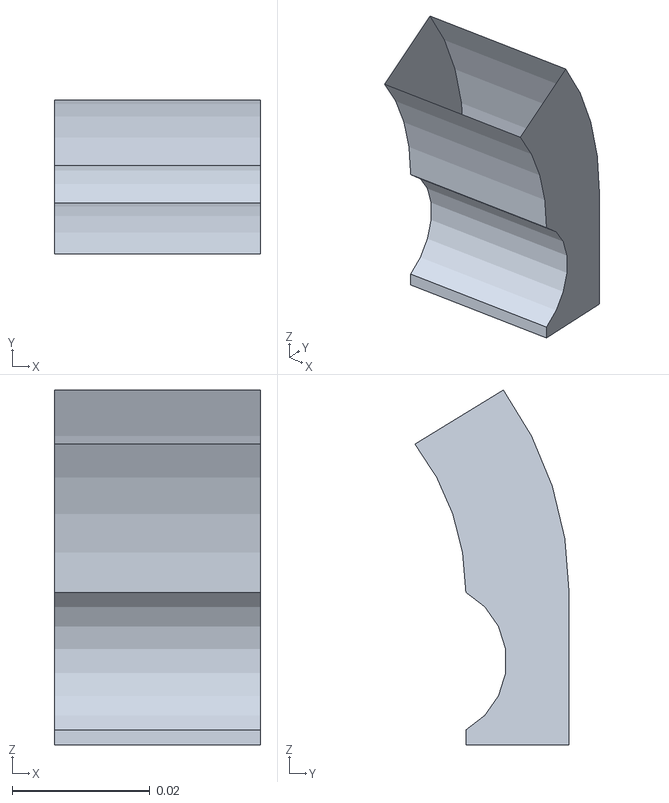
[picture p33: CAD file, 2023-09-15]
data/simulation_models/meshes/hook_2_upper.STL
0.03 x 0.0224 x 0.0516

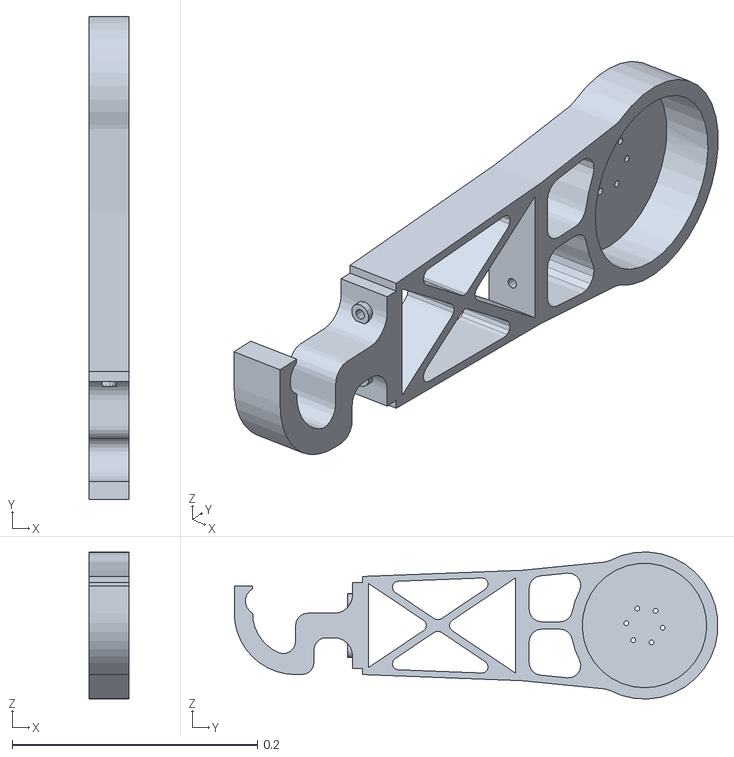
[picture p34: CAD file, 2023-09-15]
data/simulation_models/meshes/hook_1.STL
0.0325 x 0.394 x 0.12

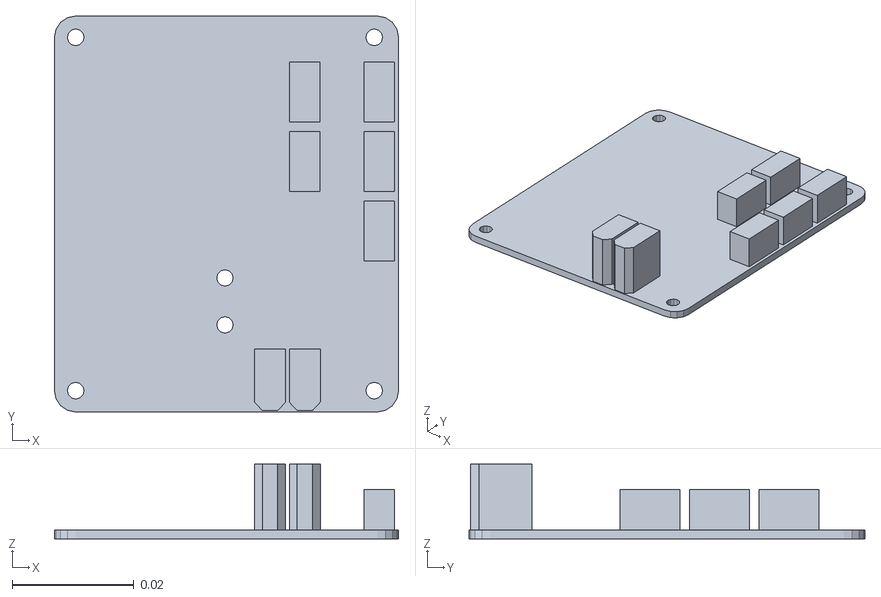
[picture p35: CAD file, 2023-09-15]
data/simulation_models/meshes/IMU.STL
0.0565 x 0.065 x 0.0123

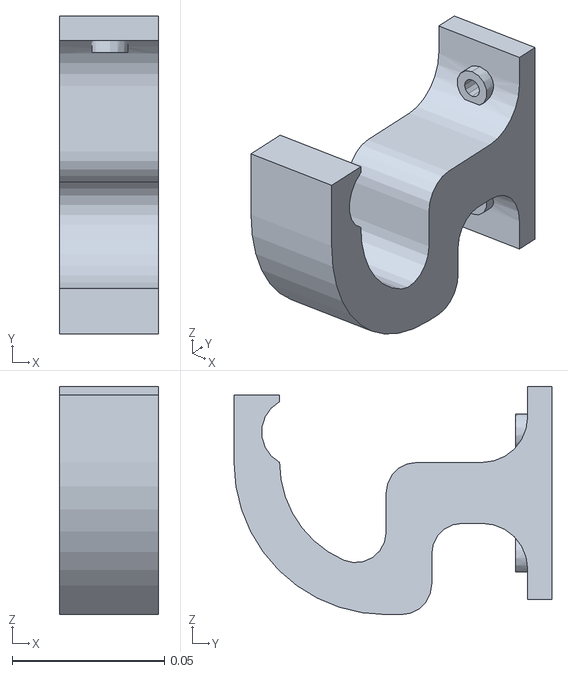
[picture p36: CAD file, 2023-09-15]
data/simulation_models/meshes/hook_2.STL
0.0324 x 0.105 x 0.075

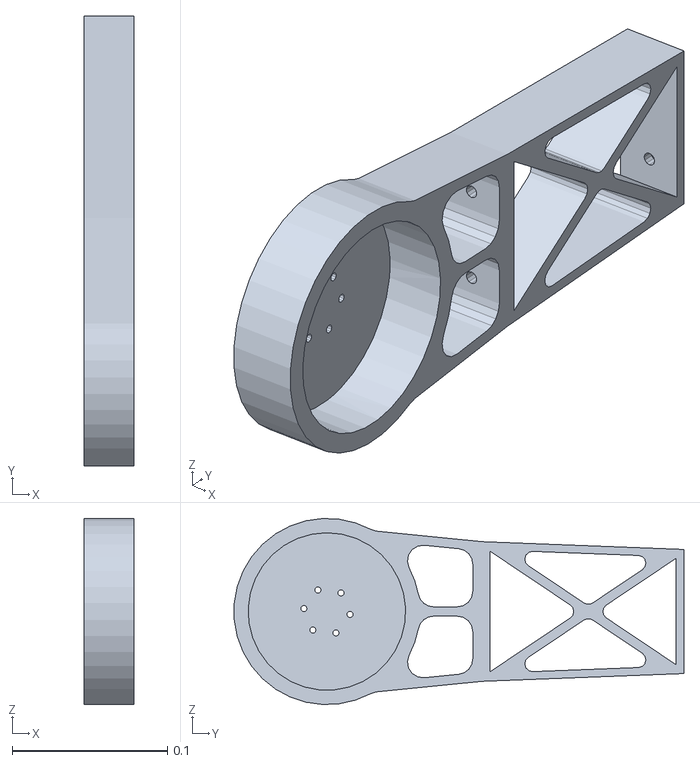
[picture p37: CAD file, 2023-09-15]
data/simulation_models/meshes/link2.STL
0.0325 x 0.29 x 0.12

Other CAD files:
data/simulation_models/meshes/stick_2.STL
data/simulation_models/meshes/Base.obj
data/simulation_models/meshes/IMU.obj
data/simulation_models/meshes/hook_1.obj
data/simulation_models/meshes/hook_2.obj
data/simulation_models/meshes/link2.obj
data/simulation_models/meshes/link_2.STL
data/simulation_models/meshes/stick_0.obj
data/simulation_models/meshes/stick_1.obj
data/simulation_models/meshes/stick_2.obj

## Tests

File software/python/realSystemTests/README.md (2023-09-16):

# Test files
This folder contains various files that can be used to test the functioning of RicMonk and all its components. The following provides information on the files. If some error arises like problem with saving or accessing files, try running the files as administrator by including `sudo` before the command used to run the file.

**Note:** With the current RicMonk, motor_9 (motor ID = 9) is attached to the left arm, and motor_8 (motor ID = 8) is attached to the right arm. The robot is said to be performing an odd brachiation if the left arm becomes the **stance arm** (the arm that holds onto the ladder bar as the rest of the robot swings) and the right arm becomes the **swing arm** (the arm the swings with the robot to help the robot brachiate forwards or backwards).

**Note:** Zero position is the position when the **stance arm** is vertically up and grasping the ladder bar, while rest of the robot hangs due to gravity. As zero position, the tail and the **swing arm** are also hanging vertically downwards.
<!---
**ADD A PICTURE OF THE ROBOT IN ZERO POSITION, maybe**
-->

## go-zero-pos.py
This file is used to command a single motor (motor ID and the bus the motor is connected to are variables in the code) to rotate from position to position. If the motor is already in some non-zero position, by changing the `final_pos` to zero and running this file, the motor returns to zero position. This file may be running using the following:
```bash
python3 -E go-zero-pos.py
```

## imu_validation_active_test.py
For testing the estimation of position and velocity of the unactuated joint using the IMU output, this code may be used. An assumption made is that an acroBot type set is used for this purpose, with the unactuated joint also attached to an actuator. The actuator attached to the unactuated joint is only used to validate the state estimation made using the IMU. The setup used is shown in the following image
Since this is an active test, the setup is made to follow a trajectory and the tracking of the same serves a reference for validating the state estimation method.
To run this file use:
```bash
sudo -E python3 imu_validation_active_test.py
```

<div align="center">
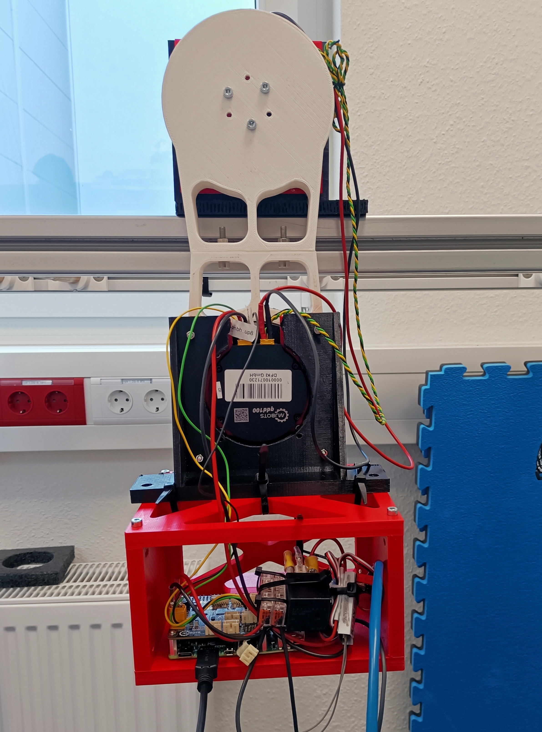
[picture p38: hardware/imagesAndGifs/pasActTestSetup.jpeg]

</div>

## imu_validation_passive_test.py
This test uses the same setup as that for the active test. However, given that this is a passive test, the motors are not given any trajectory to track. The setup needs to be manually moved, and comparision between the measured and estimated unactuated joint position and velocity may be used to validate the state estimation method.
To run the file use:
```bash
sudo -E python3 imu_validation_passive_test.py
```

## ladderReleaseLoop.py
This is an extensively written code to estimate the full state of the robot as it releases grasp from a ladder bar (front/back) for odd or even brachiations. These parameters need to set at the beginning of the code and the same continues as long as release tests are being performed.
Ensure that the robot is in the required zero position for the required type of brachiation (left arm is stance arm for odd brachiation, right arm is stance arm for even brachiation), before the code is run. Once ensured, run the code, set the robot with the required release position (swing arm on the back bar for back release test and swing arm on front bar for front release test). Reply accordingly to the question asked if the test need to be continued with. If the feed-forward torques were set as required before the code was run, then there may not be any requirement to change these values. However, if required these feed-forward torques may be varied for any iteration of the release tests. Answer accordingly to the question regarding changing these values. Subsequently, after the feed-forward the state information of the robot may be saved into an excel file based on the response to another question. Once this stage is completed, to continue with more release tests the robot may be set to release position again, and the question regarding more tests may be answered accordingly. 
Based on the information provided initially, the data from the tests are saved to respective excel files (evenBrachBackReleaseVelocities.xlsx, evenBrachFrontReleaseVelocities.xlsx, oddBrachBackReleaseVelocities.xlsx, oddBrachFrontReleaseVelocities.xlsx)
To run the cbashode:
```bash
sudo -E python3 ladderReleaseLoop.py
```

## motor_enable.py
To enable the motors, or stop them, or zero-offset both the motors, to instantly make sure that communication with the motors is intact, the following command may be used:
```bash
sudo -E python3 motor_enable.py
```

## single_odd_brachiation.py
As indicated by the name of this program, this program was used to test single odd brachiation maneuvers. To test the maneuver, firstly, the robot needs to be placed in the odd zero position. If testing the **BF** or **FB** trajectory, ensure that the proper feed-forward torque values are set in the function call of `kickback` function in the `brachiation` function. 
- Once set in the odd zero position (left arm hanging from support bar, right arm and tail vertically downwards), navigate to the current folder via terminal
- Ensure that the Makefile is set to run `single_odd_brachiation.py`.
- Turn ON the motors using the safety switch. Keep the safety switch close to you at all times
- Run the following snippet to enable the robot to perform the **BF** maneuver, and also informing that the motors are connected Bus 4 instead of 2. To enable the robot to perform other maneuvers, replace the `MANEUVER` field with appropriate maneuver name.
```bash
make BUS_NUMBER=4 MANEUVER=BF
```
- If the maneuver requested is either **BF** or **FB**, once the motors are calibrated, when the prompt asks if the robot is set at the required initial position, manually move the robot right arm to place the robot in a double support configuration. When done, input `y`.
- The robot would ideally perform the required maneuver
- If the robot behaves erratically or unsuccessfully performs a maneuver, immediately switch OFF the motors using the remote safety switch.

## read_imu.py
This program is run to test the functioning of the IMU. The configuration of the IMU may be modified as required in the code. Running this code continuously returns all the information from the IMU output continuously at a high frequency until the code is aborted. To run, use:
```bash
sudo -E python3 read_imu.py
```

## read_motor_data.py
This code runs to read and save the position and velocity values of a motor (motor ID and bus number are variables) over a certain period of time. The data is saved in a .csv and data is also presented in plots. To run, use:
```bash
sudo -E python read_motor_data.py
```

## tableTestMotorKickBack_try.py
Since release tests involve very high torques, the release (a.k.a kickback) functions may be tested, for a single motor, using this program, in such a way that robot arms are not connected. What is the purpose of this code when ladderReleaseLoop.py (arms dismantled) is present? Don't really know. Sorry. Run by using:
```bash
sudo -E python tableTestMotorKickBack_try.py
```

## test_multiple_brachiations.py
Already wrote about this [here](multipleBrachiationRealize.md)

## testOddEvenSwitches.py
This program is used to inspect if the changes between odd and even brachiation, if changes to be made as a result of the actuators completing a full rotation; are being handled properly during multiple brachiations (three motions is set to be a default, can be varied in line 208). During the code run, the motors don't supply any torque, and their position and velocities are read, and the state estimation is performed. The robot arms are to be manually passively moved to simulate the brachiation behaviour. The program prints a few lines to indicate start and end of a maneuver to help the user. Finally, a plot and .csv are output which can be used to validate the state estimation method. Before running the program, ensure that the robot is in odd zero position. Run the code using the following command and start moving the arms manually as required to imitate required maneuvers. Suggest to start with **ZF** trajectory, followed by successive **BF** maneuvers.
```bash
sudo -E python3 testOddEvenSwitches.py
```

## trajectory_replay.py
To test the trajectories without applying a controller, this program may be used, by running the following command:
```bash
sudo -E python3 trajectory_replay.py
```

## single_even_brachiation.py
This code is similar to the `single_odd_brachiation.py` code. Replace odd with even in the Makefile. Before running the code, place the robot in even zero position (right arm hanging from support bar, left arm and tail vertically downwards). Other steps are similar.

## two_motor_goto_pos.py
This program does exactly what the name of the program describes. It commands, once, two motors to go to a specified position. Run, using:
```bash
sudo -E python two_motor_goto_pos.py
```

## utils.py
This file contains all the required functions for the RicMonk to do what it does.

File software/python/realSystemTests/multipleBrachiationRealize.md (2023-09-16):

# Realizing Multiple brachiation on the RicMonk

## Forward brachiation
The following steps help in realizing the multiple brachiation motion, in the forward direction, on the RicMonk:
- Trajectories stabilized are stored [here](/data/trajectories/closed_loop) with respect to the current file
- The program to be run for executing multiple brachiaitions in the forward direction is **test_multiple_brachiations.py**
- Ensure that RicMonk is on the ladder, with left arm on the ladder, while right arm and the tail are vertical
- Ensure that all the electrical connections are properly made, and that the motors are turned ON using the transmitter
- Via terminal, navigate to the folder of the current file (the folder that also contains **test_multiple_brachiations.py**) on the Raspberry Pi terminal
- Open the **Makefile** and ensure that the python code set to run is `test_multiple_brachiations.py`.
- Ensure that all parameters are properly set.
- Keep the safety switch close to you at all times
- If the parameters in the Makefile were not set right, the information can also be given in the command line as follows. The following enables RicMonk to perform three (change `NBRACH` value in command line for more number) multiple brachiation maneuvers (one **ZB**, followed by two **FB**) in the backward direction (`DIRECTION=-1`). It also changes the `BUS_NUMBER` parameter to 3 instead of 2. (To enable the robot to perform multiple forward brachiation maneuvers, `DIRECTION` must be set to 1).
```bash
make NBRACH=3 BUS_NUMBER=3 DIRECTION=-1
```
- If the robot behaves erratically or unsuccessfully performs a maneuver, immediately switch OFF the motors using the remote safety switch.

- Information regarding testing single brachiation maneuvers and other tests are provided in [here](README.md)

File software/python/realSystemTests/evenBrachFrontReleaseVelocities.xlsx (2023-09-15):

 |  |  |  |  | EVEN BRACHIATION FRONT RELEASE
TRIAL |  | ARM1 POSITION | ARM1 VELOCITY | TAIL POSITION | TAIL VELOCITY | TAIL TORQUE | ARM2 POSITION | ARM2 VELOCITY | ARM2 TORQUE
O | O | O | O | O | O | O | O | O | O

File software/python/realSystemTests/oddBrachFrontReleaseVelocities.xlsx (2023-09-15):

 |  |  |  |  | ODD BRACHIATION FRONT RELEASE
TRIAL |  | ARM1 POSITION | ARM1 VELOCITY | TAIL POSITION | TAIL VELOCITY | TAIL TORQUE | ARM2 POSITION | ARM2 VELOCITY | ARM2 TORQUE
O | O | O | O | O | O | O | O | O | O
0 | 0 | 0 | 0 | 0 | 0 | 0 | 0 | 0 | 0

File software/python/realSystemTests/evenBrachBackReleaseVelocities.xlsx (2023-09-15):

 |  |  |  |  | EVEN BRACHIATION BACK RELEASE
TRIAL |  | ARM1 POSITION | ARM1 VELOCITY | TAIL POSITION | TAIL VELOCITY | TAIL TORQUE | ARM2 POSITION | ARM2 VELOCITY | ARM2 TORQUE
O | O | O | O | O | O | O | O | O | O
1 |  | -2.425394619 | 3.495470054 | 2.488979702 | -2.139952634 | -0.3718525767 | -0.685305917 | 0.4540012945 | -0.1238417327
2 |  | -2.433990751 | 2.634389679 | 2.493006402 | -1.411318501 | -0.3437802196 | -0.6780195082 | 0.2102315801 | -0.4020914137
3 |  | -2.429362273 | 3.164455367 | 2.472872904 | -1.971994096 | -0.3749627173 | -0.6617209624 | 0.254755761 | -0.09126382321
4 |  | -2.411000213 | 3.516104155 | 2.475461496 | -2.077252667 | -0.2476459891 | -0.6924005781 | 0.8328946428 | -0.2889650166
5 |  | -2.419859204 | 3.101107944 | 2.444781881 | -1.885770969 | -0.3220513165 | -0.6460935331 | 0.03518636019 | -0.4126171172
6 |  | -2.409769647 | 3.460059744 | 2.460217562 | -2.167996095 | -0.3423567116 | -0.6708289733 | 0.1648988502 | -0.3747412562
7 |  | -2.402293672 | 3.310294047 | 2.518892328 | -2.105867626 | -0.274410665 | -0.7384200018 | 0.4036363722 | -0.3596643806
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

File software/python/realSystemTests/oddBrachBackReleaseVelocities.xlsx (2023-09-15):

 |  |  |  | ODD BRACHIATION BACK RELEASE
TRIAL | ARM1 POSITION | ARM1 VELOCITY | TAIL POSITION | TAIL VELOCITY | TAIL TORQUE | ARM2 POSITION | ARM2 VELOCITY | ARM2 TORQUE
0 | 0 | 0 | 0 | 0 | 0 | 0 | 0 | 0
1 | -0.5945001396 | -0.5274281245 | 0.7168483969 | -0.03277480411 | 0.4743259847 | -2.512468783 | 1.965665302 | 0.2710714042
2 | -0.5957482148 | -0.5420278379 | 0.6699661091 | -0.624466314 | 0.2811390162 | -2.445644745 | 1.825191461 | 0.2029676437
3 | -0.5871488858 | -0.4248546775 | 0.6552974178 | -0.4646511509 | 0.339366883 | -2.435769744 | 2.19058561 | 0.3038770258
4 | -0.5806888493 | -0.3730976418 | 0.6669940213 | -0.4338836196 | 0.298715651 | -2.449863192 | 2.691256753 | 0.3480286896
5 | -0.5837406326 | -0.320028835 | 0.67907412 | -0.1309864079 | 0.3139173985 | -2.47201004 | 1.982032757 | 0.2319043428
6 | -0.5828067935 | -0.5827245679 | 0.708219755 | -0.03911747854 | 0.5188949704 | -2.50709985 | 1.869460439 | 0.217819199
7 | -0.5816173579 | -0.4211598473 | 0.6641178074 | -0.2343215106 | 0.3580422997 | -2.459546446 | 1.738949982 | 0.4441739917
8 | -0.5828587199 | -0.4599836968 | 0.678115382 | -0.1940635968 | 0.3264121711 | -2.468654457 | 1.880046254 | 0.3686084151
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

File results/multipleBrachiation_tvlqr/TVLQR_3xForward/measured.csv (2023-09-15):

meas_time | arm1_des_Ang_pos_store | arm1_meas_Ang_pos | arm1_des_Ang_vel_store | arm1_meas_Ang_vel | tail_des_Ang_pos_store | tail_meas_Ang_pos | tail_des_Ang_vel_store | tail_meas_Ang_vel | tail_des_tau_store | tail_meas_tau | tail_cmd_tau | tail_clipped_tau | phi_des_Ang_pos_store | phi_meas_Ang_pos | phi_des_Ang_vel_store | phi_meas_Ang_vel | phi_des_tau_store | phi_meas_tau | phi_cmd_tau | phi_clipped_tau | arm2_des_Ang_vel_store | arm2_meas_Ang_pos | arm2_des_Ang_pos_store | arm2_meas_Ang_vel | raw_imu_pos | raw_imu_vel | k1_store | k2_store | k3_store | k4_store | k5_store | k6_store | k7_store | k8_store | k9_store | k10_store | k11_store | k12_store | state_machine_flag
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

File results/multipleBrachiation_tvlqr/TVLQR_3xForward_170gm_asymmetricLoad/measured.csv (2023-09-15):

meas_time | arm1_des_Ang_pos_store | arm1_meas_Ang_pos | arm1_des_Ang_vel_store | arm1_meas_Ang_vel | tail_des_Ang_pos_store | tail_meas_Ang_pos | tail_des_Ang_vel_store | tail_meas_Ang_vel | tail_des_tau_store | tail_meas_tau | tail_cmd_tau | tail_clipped_tau | phi_des_Ang_pos_store | phi_meas_Ang_pos | phi_des_Ang_vel_store | phi_meas_Ang_vel | phi_des_tau_store | phi_meas_tau | phi_cmd_tau | phi_clipped_tau | arm2_des_Ang_vel_store | arm2_meas_Ang_pos | arm2_des_Ang_pos_store | arm2_meas_Ang_vel | raw_imu_pos | raw_imu_vel | k1_store | k2_store | k3_store | k4_store | k5_store | k6_store | k7_store | k8_store | k9_store | k10_store | k11_store | k12_store | state_machine_flag
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

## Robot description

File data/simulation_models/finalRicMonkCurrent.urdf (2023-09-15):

<?xml version="1.0" encoding="utf-8"?>
<!-- This URDF was automatically created by SolidWorks to URDF Exporter! Originally created by Stephen Brawner (brawner@gmail.com) 
     Commit Version: 1.6.0-1-g15f4949  Build Version: 1.6.7594.29634
     For more information, please see http://wiki.ros.org/sw_urdf_exporter -->
<robot name="ricMonk">
  
	<link name="Base">
		<inertial>
		<origin xyz="0.0536 0.69428 -0.16917" rpy="0 0 0" />
		<mass value="5.9209" />
		<inertia ixx="0.86611" ixy="3.0201E-12" ixz="-8.3865E-08" iyy="0.13388" iyz="2.0135E-12" izz="0.76254" />
		</inertial>
		<visual>
		<origin xyz="0 0 0" rpy="0 0 0" />
		<geometry>
		<mesh filename="meshes/Base.obj" />
		</geometry>
		<material name="">
		<color rgba="1 0.70980 0.50196 0.8" />
		</material>
		</visual>
	</link>  
	
	<joint name="base_weld" type="fixed">
	      <origin xyz="0 0 0" rpy="0 0 0" /> 
	      <parent link="world"/>
	      <child link="Base"/>
  	</joint>  
  
	<link name="stick_2">
		<inertial>
		<origin xyz="0.0536 0 0" rpy="0 0 0" />
			<mass value="0.062168" />
		<inertia ixx="4.4463E-06" ixy="-1.0251E-21" ixz="1.5345E-20" iyy="0.00084889" iyz="-2.4293E-22" izz="0.00084889" />
		</inertial>
		<visual>
			<origin xyz="0 0 0" rpy="0 0 0" />
			<geometry>
			<mesh filename="meshes/stick_2.obj" />
			</geometry>
			<material name="">
			<color rgba="1 1 1 1" />
			</material>
		</visual>
	</link>
  

	<joint name="stick_2" type="fixed">
		<origin xyz="0 0.34 0" rpy="0 0 0" />
		<parent link="Base" />
		<child link="stick_2" />
		<axis xyz="0 0 0" />
	</joint>  
  
	<link name="stick_1">
		<inertial>
			<origin xyz="0 0 0" rpy="0 0 0" />
			<mass value="0" />
			<inertia ixx="0" ixy="0" ixz="0" iyy="0" iyz="0" izz="0" />
		</inertial>
		<visual>
			<origin xyz="0 0 0" rpy="0 0 0" />
			<geometry>
			<mesh filename="meshes/stick_1.obj" />
			</geometry>
			<material name="">
			<color rgba="1 1 1 1" />
		</material>
		</visual>
	</link>
	<joint name="stick_1" type="fixed">
		<origin xyz="0 -0.34 0" rpy="0 0 0" />
		<parent link="Base" />
		<child link="stick_1" />
		<axis xyz="0 0 0" />
	</joint>
  
	<link name="stick_0">
		<inertial>
			<origin xyz="0 0 0" rpy="0 0 0" />
			<mass value="0" />
			<inertia ixx="0" ixy="0" ixz="0" iyy="0" iyz="0" izz="0" />
			</inertial>
		<visual>
			<origin xyz="0 0 0" rpy="0 0 0" />
			<geometry>
			<mesh filename="meshes/stick_0.obj" />
			</geometry>
			<material name="">
			<color rgba="1 1 1 1" />
			</material>
		</visual>
	</link>
	<joint name="stick_0" type="fixed">
		<origin xyz="0 0 0" rpy="0 0 0" />
		<parent link="Base" />
		<child link="stick_0" />
		<axis xyz="0 0 0" />
	</joint>
  
	<link name="hook_1">
	<inertial>
		<origin xyz="-0.00077047 0.16959 -0.022094" rpy="0 0 0" />
		<mass value="0.31253" />
		<inertia ixx="0.00099006" ixy="6.8261E-06" ixz="1.0342E-10" iyy="0.00036755" iyz="-4.7577E-06" izz="0.00069232" />
	</inertial>
	<visual>
		<origin xyz="0 0 0" rpy="0 0 0" />
		<geometry>
		<mesh filename="meshes/hook_1.obj" />
		</geometry>
		<material name="">
		<color rgba="0.96078 0.15294 0.15294 0.8" />
		</material>
	</visual>
	<!--
	<collision>
		<origin xyz="0 0 0" rpy="0 0 0" />
		<geometry>
		<mesh filename="meshes/hook_1.obj" />
		</geometry>
	</collision>
	-->
	</link>
	
	<link name="tail">
		<inertial>
			<origin xyz="-0.0056009765606122 0.182449040804017 0.00254813231558806" rpy="0 0 0" />
			      <mass value="2.63096785521702" />
			      <inertia ixx="0.00523785541666047" ixy="5.87184699597149E-07" ixz="-4.07133795898078E-07" iyy="0.00395069160539681" iyz="-1.24226112383513E-06" izz="0.00309094774503178" />
			</inertial>
		<visual>
			<origin xyz="0 0 0" rpy="0 0 0" />
			<geometry>
			<mesh filename="meshes/tail.obj" />
			</geometry>
			<material name="">
			<color rgba="0.42352 0.96078 0.12594 0.8" />
			</material>
		</visual>
		<!--
		<collision>
			<origin xyz="0 0 0" rpy="0 0 0" />
			<geometry>
			<mesh filename="meshes/tail.obj" />
			</geometry>
		</collision>
		-->
	</link>
  
	<link name="link2">
		<inertial>
			<origin xyz="-0.0011371 0.089177 -1.9429E-16" rpy="0 0 0" />
			<mass value="0.140647941711974" />
			<inertia ixx="0.0008365" ixy="-6.8246E-06" ixz="-2.7105E-20" iyy="0.00032416" iyz="-1.152E-19" izz="0.00056305" />
			</inertial>
		<visual>
			<origin xyz="0 0 0" rpy="0 0 0" />
			<geometry>
			<mesh filename="meshes/link2.obj" />
			</geometry>
			<material name="">
			<color rgba="0.15294 0.67450 0.96078 0.8" />
			</material>
		</visual>
		<!--
		<collision>
			<origin xyz="0 0 0" rpy="0 0 0" />
			<geometry>
			<mesh filename="meshes/link2.obj" />
			</geometry>
		</collision>
		-->
	</link>

	<link name="hook_2">
		<inertial>
			<origin xyz="-1.4364E-07 0.035208 -0.027189" rpy="0 0 0" />
			<mass value="0.171894025592926" />
			<inertia ixx="0.00015356" ixy="1.4986E-09" ixz="1.0342E-10" iyy="4.3392E-05" iyz="-4.7577E-06" izz="0.00012928" />
			</inertial>
		<visual>
			<origin xyz="0 0 0" rpy="0 0 0" />
			<geometry>
			<mesh filename="meshes/hook_2.obj" />
			</geometry>
			<material name="">
			<color rgba="0.15294 0.67450 0.96078 0.8" />
			</material>
		</visual>
		<!--
		<collision>
			<origin xyz="0 0 0" rpy="0 0 0" />
			<geometry>
			<mesh filename="meshes/hook_2.obj" />
			</geometry>
		</collision>
		-->
	</link>
  
	<joint name="virtual_fixed_link" type="fixed">
		<origin xyz="0.00054999999999894 0.314008861212629 0.0200000000000001" rpy="0 0 -3.14159265358979" />
		<parent link="link2" />
		<child link="hook_2" />
		<axis xyz="0 0 0" />
	</joint>

	<joint name="virtul_joint_hook_1" type="revolute">
		<origin xyz="0 0 0" rpy="-1.5708 0 0" />
		<parent link="Base" />
		<child link="hook_1" />
		<axis xyz="1 0 0" />
		<limit lower="-3.1415926" upper="3.1415926" effort="16" velocity="43" />
	</joint>
  
	<joint name="Joint1" type="revolute">
		<origin xyz="0.0365499999999668 0.31400886121263 -0.019999999999951" rpy="-3.14159265358979 0 3.14159265358979" />
		<parent link="hook_1" />
		<child link="tail" />
		<axis xyz="-1 0 0" />
		<limit lower="-3.1415926" upper="3.1415926" effort="16" velocity="43" />
	</joint>
	 <!--
	<joint name="Joint2" type="revolute">
		<origin xyz="0.0730499999999658 0.31400886121263 -0.0199999999999525" rpy="-3.14159265358979 0 3.14159265358979" />
		<parent link="hook_1" />
		<child link="link2" />
		<axis xyz="-1 0 0" />
		<limit lower="-3.1415926" upper="3.1415926" effort="16" velocity="43" />
	</joint>
	-->
	
	<joint name="Joint3" type="revolute">
		<origin xyz="-0.0365 0 0" rpy="0 0 0" />
		<parent link="tail" />
		<child link="link2" />
		<axis xyz="-1 0 0" />
		<limit lower="-3.1415926" upper="3.1415926" effort="16" velocity="43" />
	</joint>	
 
	<transmission type="SimpleTransmission" name="hook1_tail">
		<actuator name="Joint1"/>
		<joint name="Joint1"/>
		<mechanicalReduction>1</mechanicalReduction>
	</transmission>  
	 <!--
	<transmission type="SimpleTransmission" name="hook1_hook2">
		<actuator name="Joint2"/>
		<joint name="Joint2"/>
		<mechanicalReduction>1</mechanicalReduction>
	</transmission> 
	-->
	<transmission type="SimpleTransmission" name="tail_hook2">
		<actuator name="Joint3"/>
		<joint name="Joint3"/>
		<mechanicalReduction>1</mechanicalReduction>
	</transmission>  
</robot>

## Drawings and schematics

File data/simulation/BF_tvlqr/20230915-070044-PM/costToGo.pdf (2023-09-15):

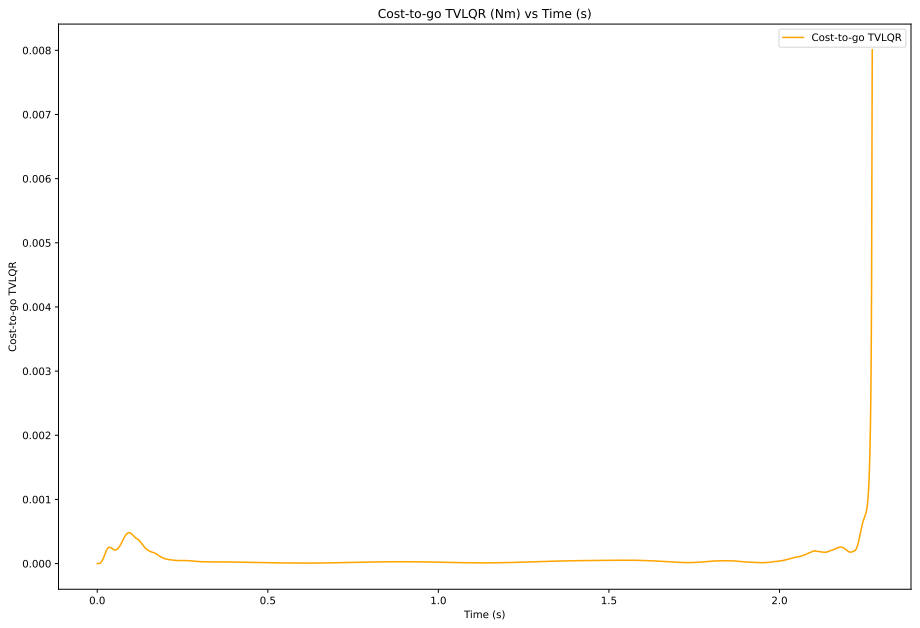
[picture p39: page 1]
Time (s)

Cost-to-go TVLQR (Nm) vs Time (s)

Cost-to-go TVLQR

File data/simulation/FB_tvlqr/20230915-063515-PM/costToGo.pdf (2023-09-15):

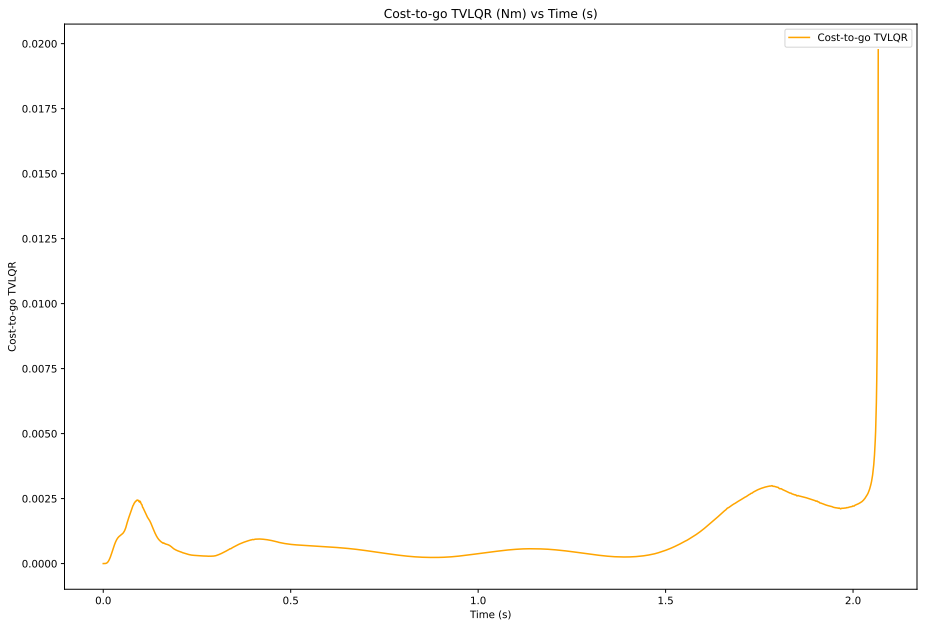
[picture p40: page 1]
Time (s)

Cost-to-go TVLQR (Nm) vs Time (s)

Cost-to-go TVLQR

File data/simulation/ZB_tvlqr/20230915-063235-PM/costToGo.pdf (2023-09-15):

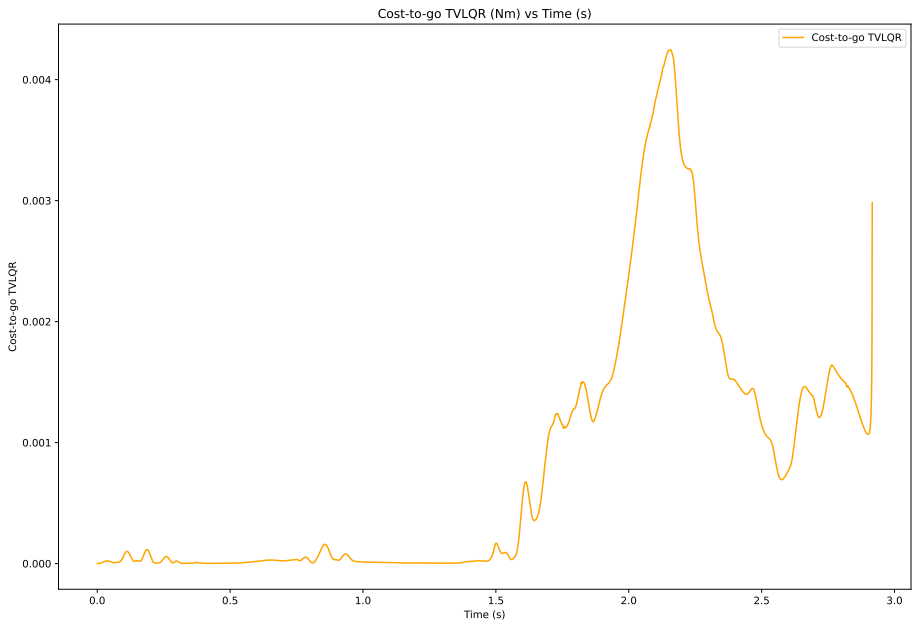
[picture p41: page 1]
Time (s)

Cost-to-go TVLQR (Nm) vs Time (s)

Cost-to-go TVLQR

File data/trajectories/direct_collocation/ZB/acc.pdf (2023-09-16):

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

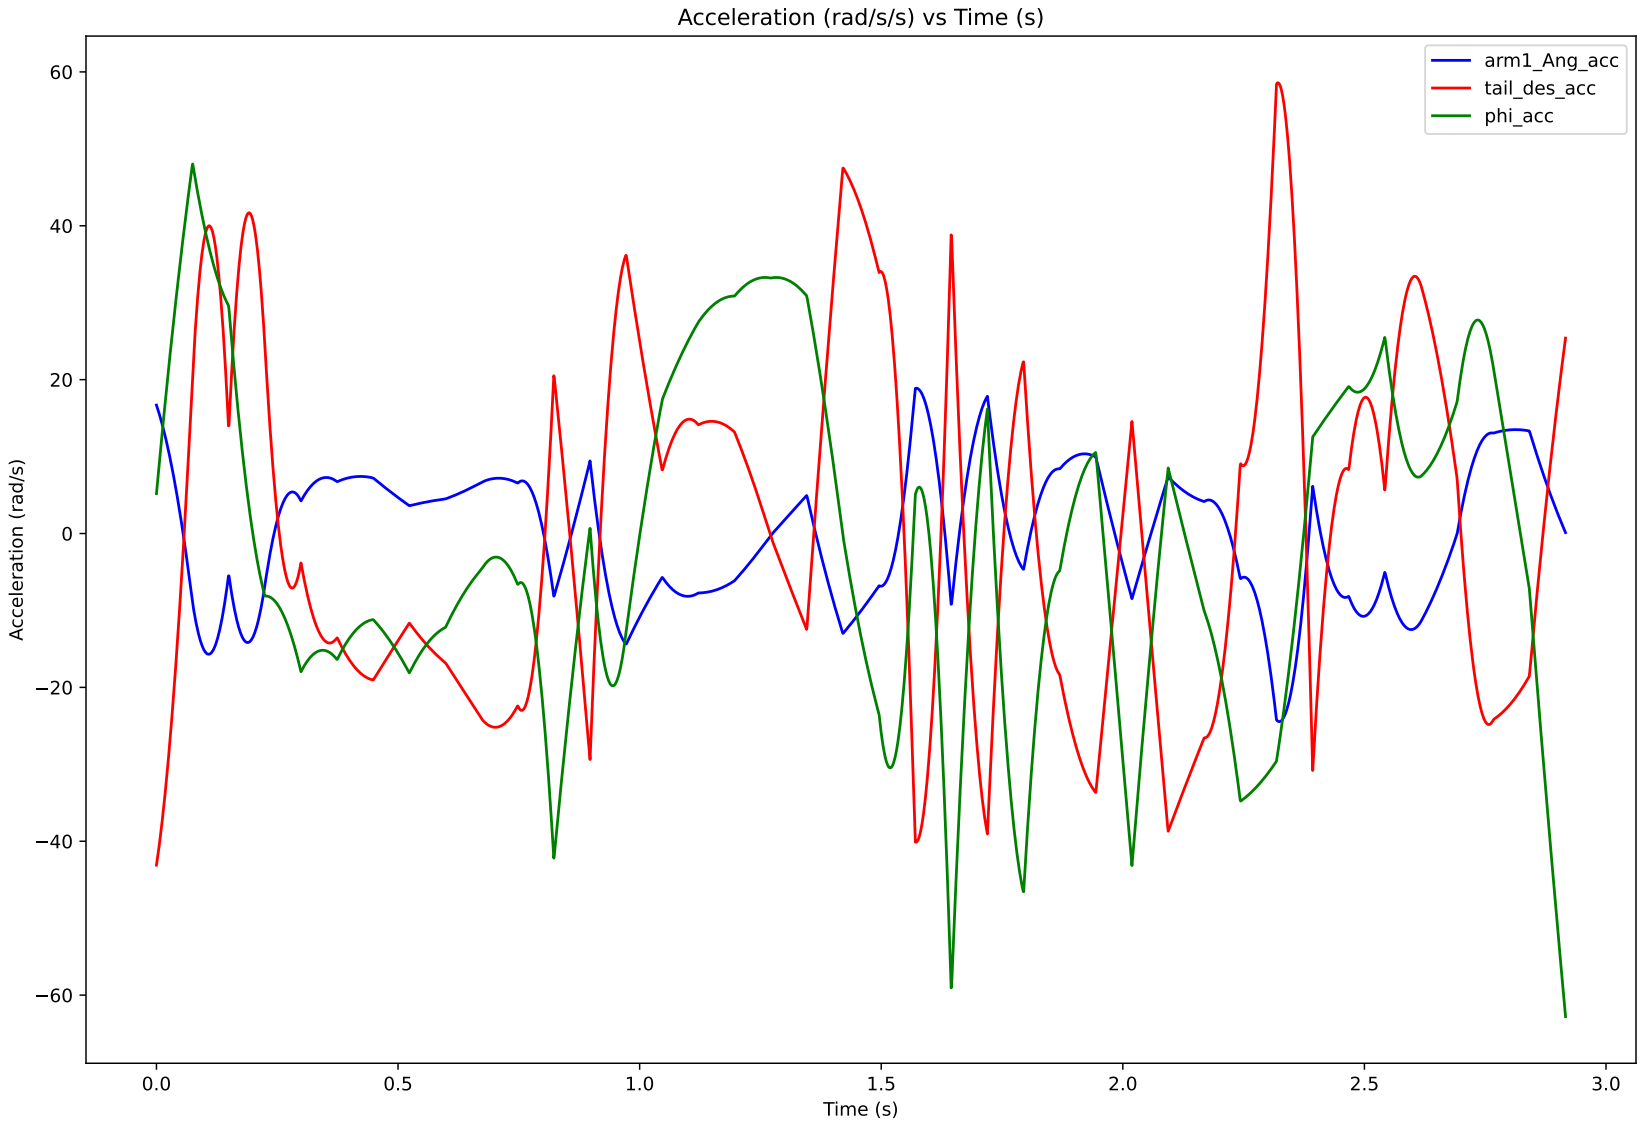
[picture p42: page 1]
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

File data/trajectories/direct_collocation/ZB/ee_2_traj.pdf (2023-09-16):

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

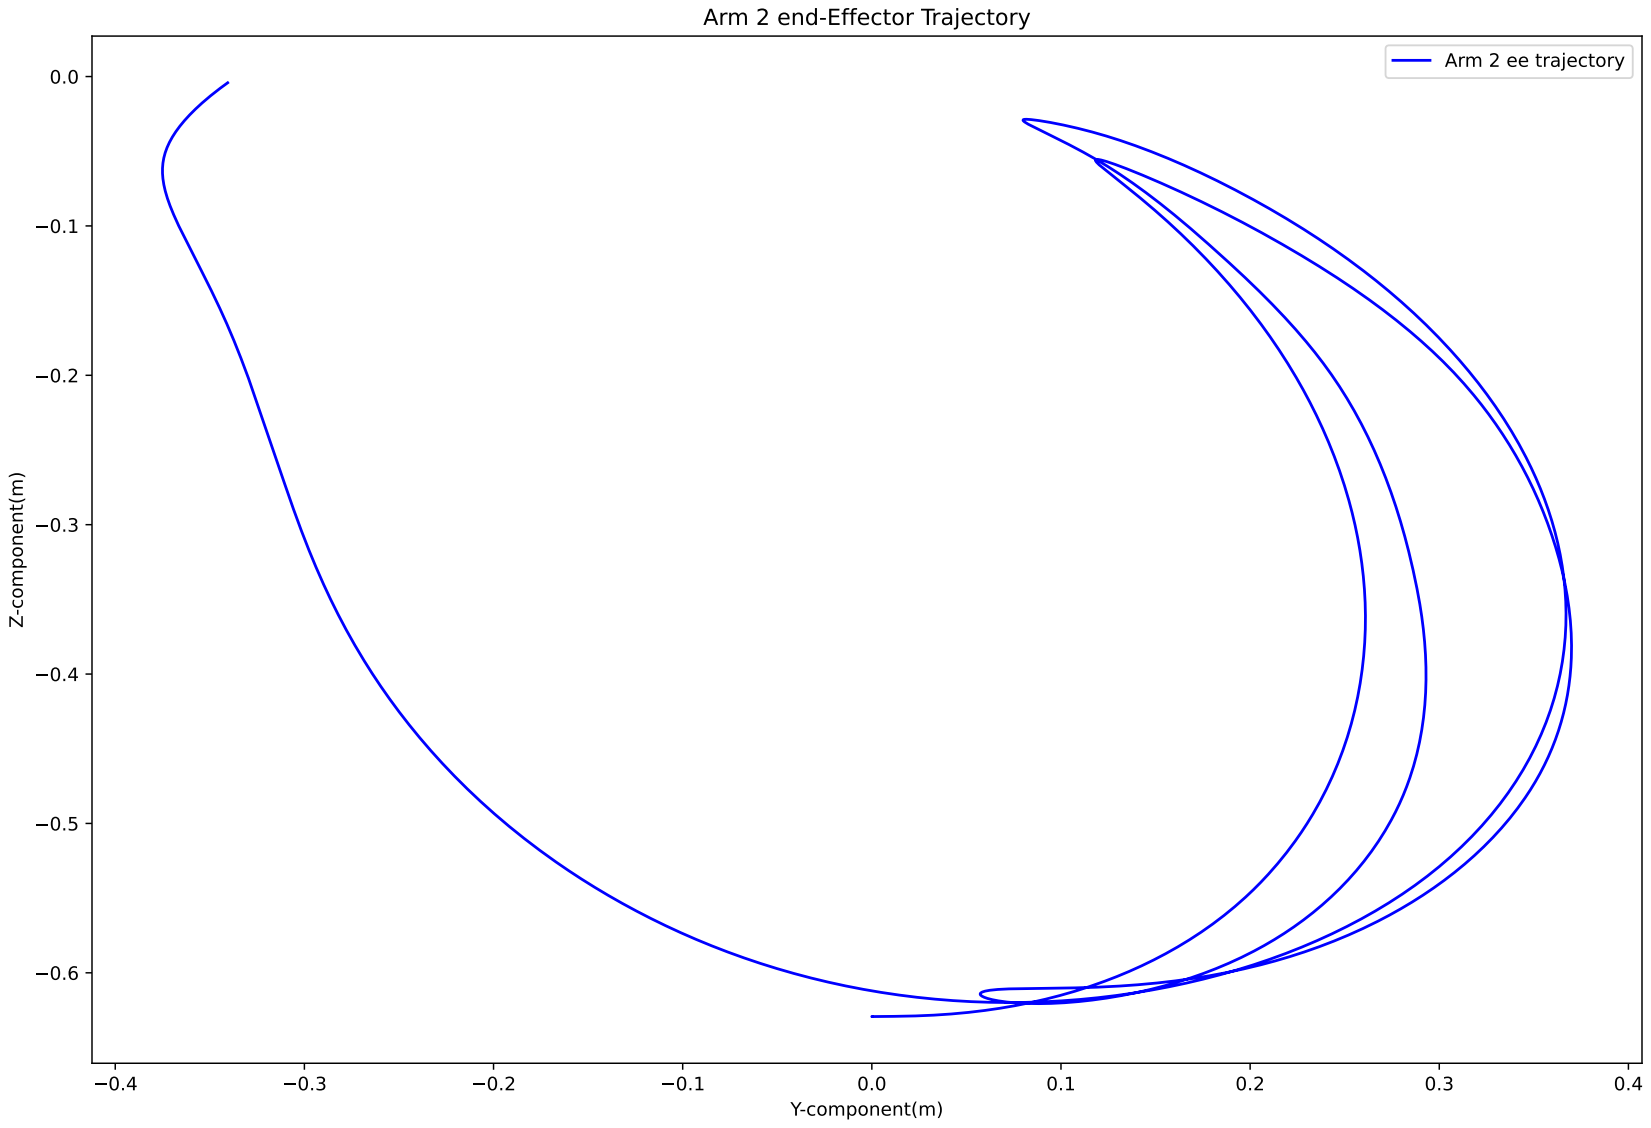
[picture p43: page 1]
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

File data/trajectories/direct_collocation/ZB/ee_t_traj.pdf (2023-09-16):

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

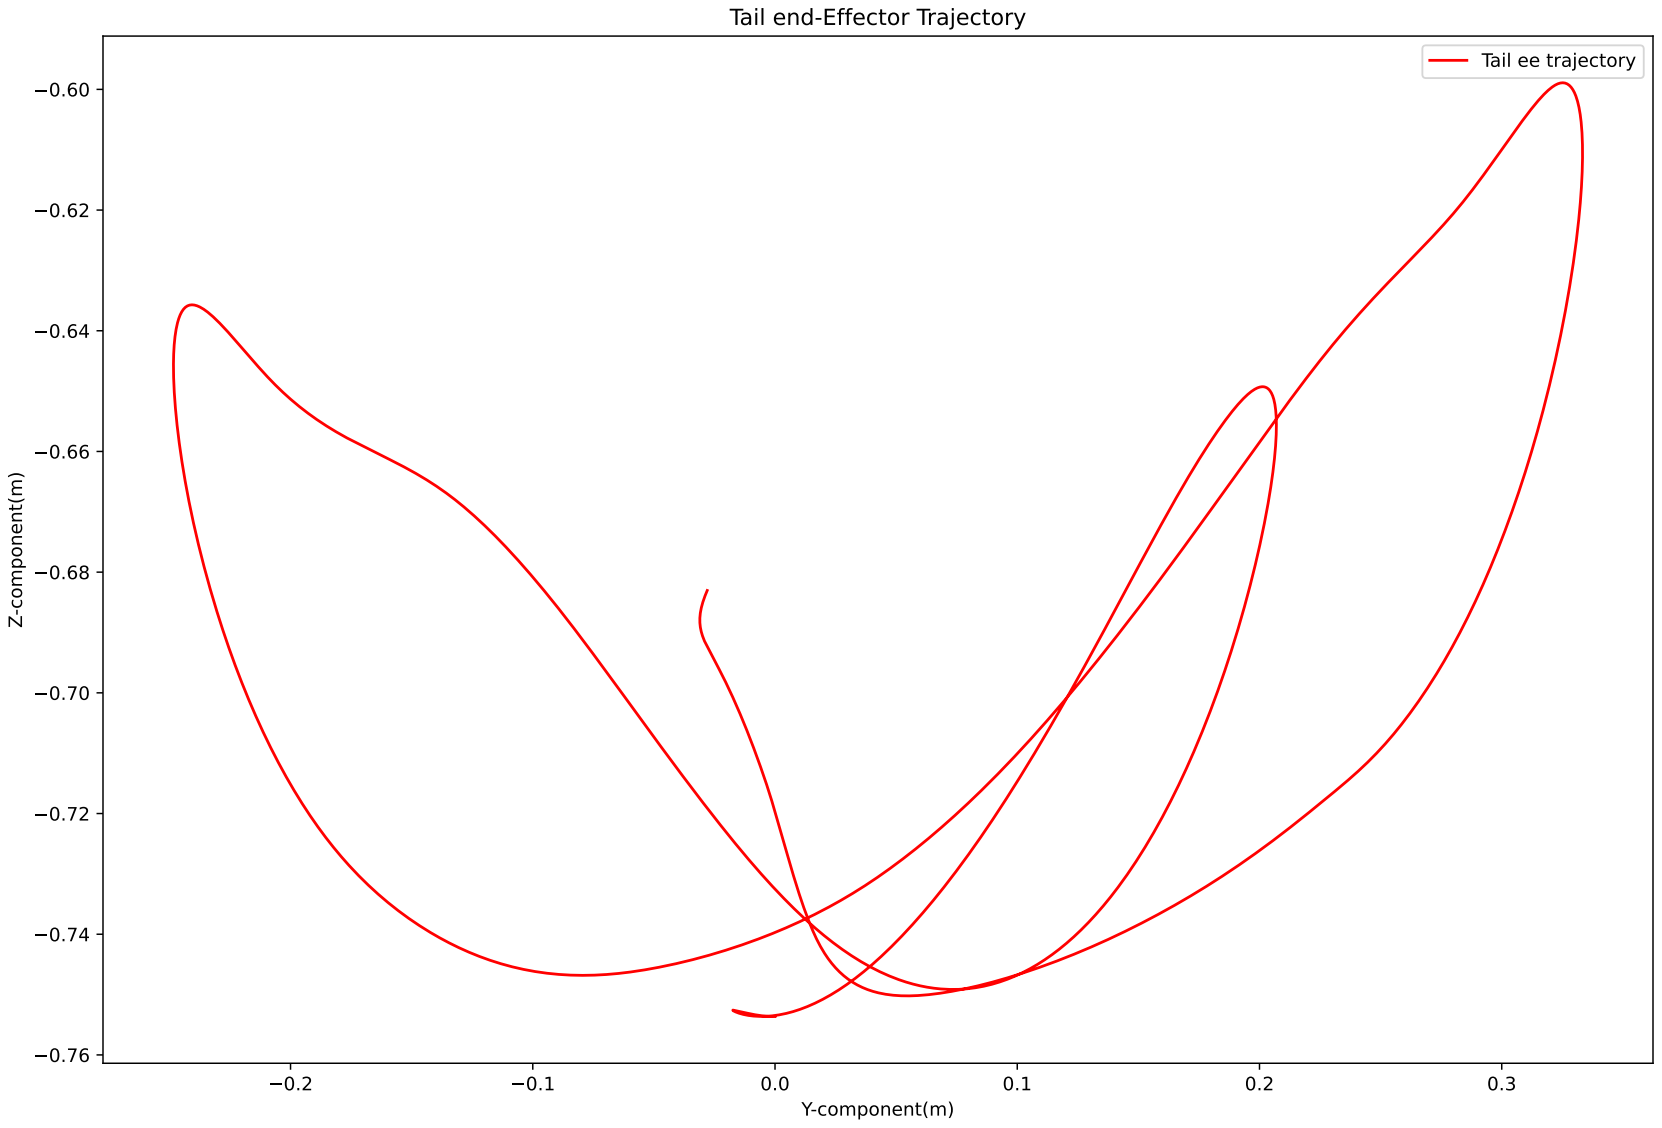
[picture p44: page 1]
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

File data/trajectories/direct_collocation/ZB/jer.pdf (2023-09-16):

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

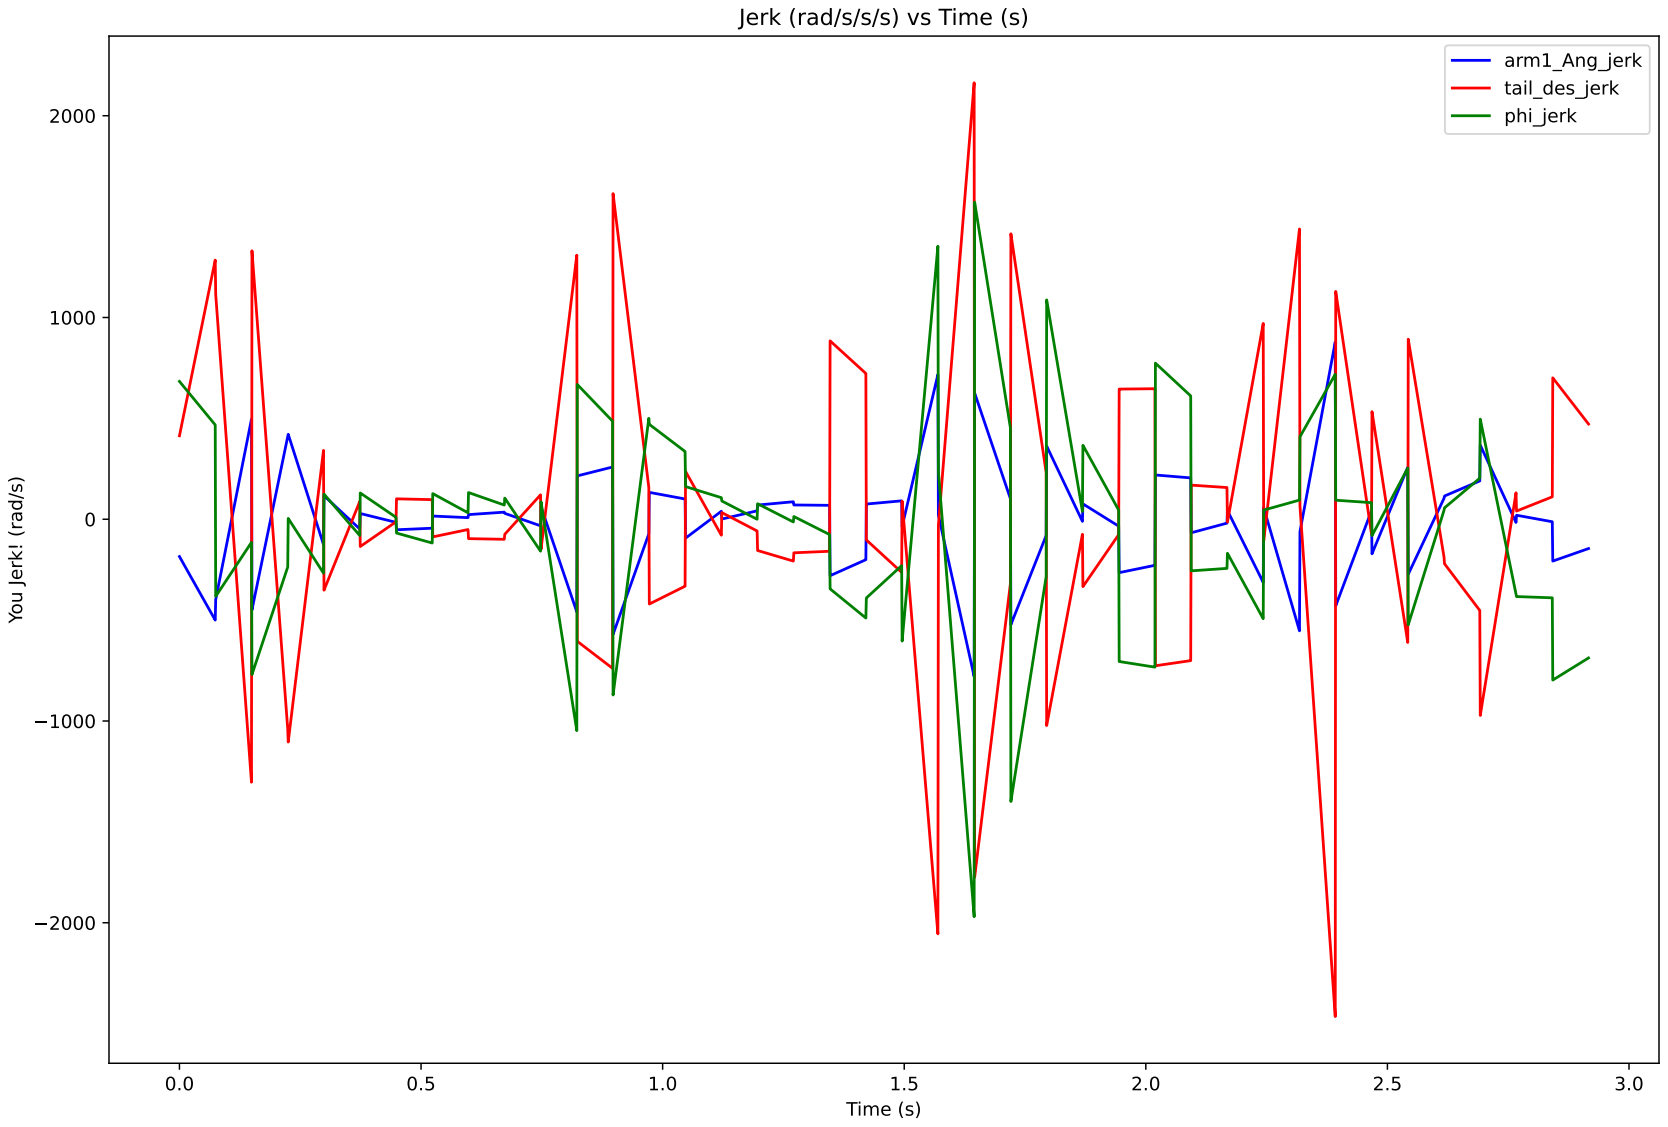
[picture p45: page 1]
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

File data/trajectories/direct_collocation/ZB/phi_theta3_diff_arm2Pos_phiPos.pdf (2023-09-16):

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

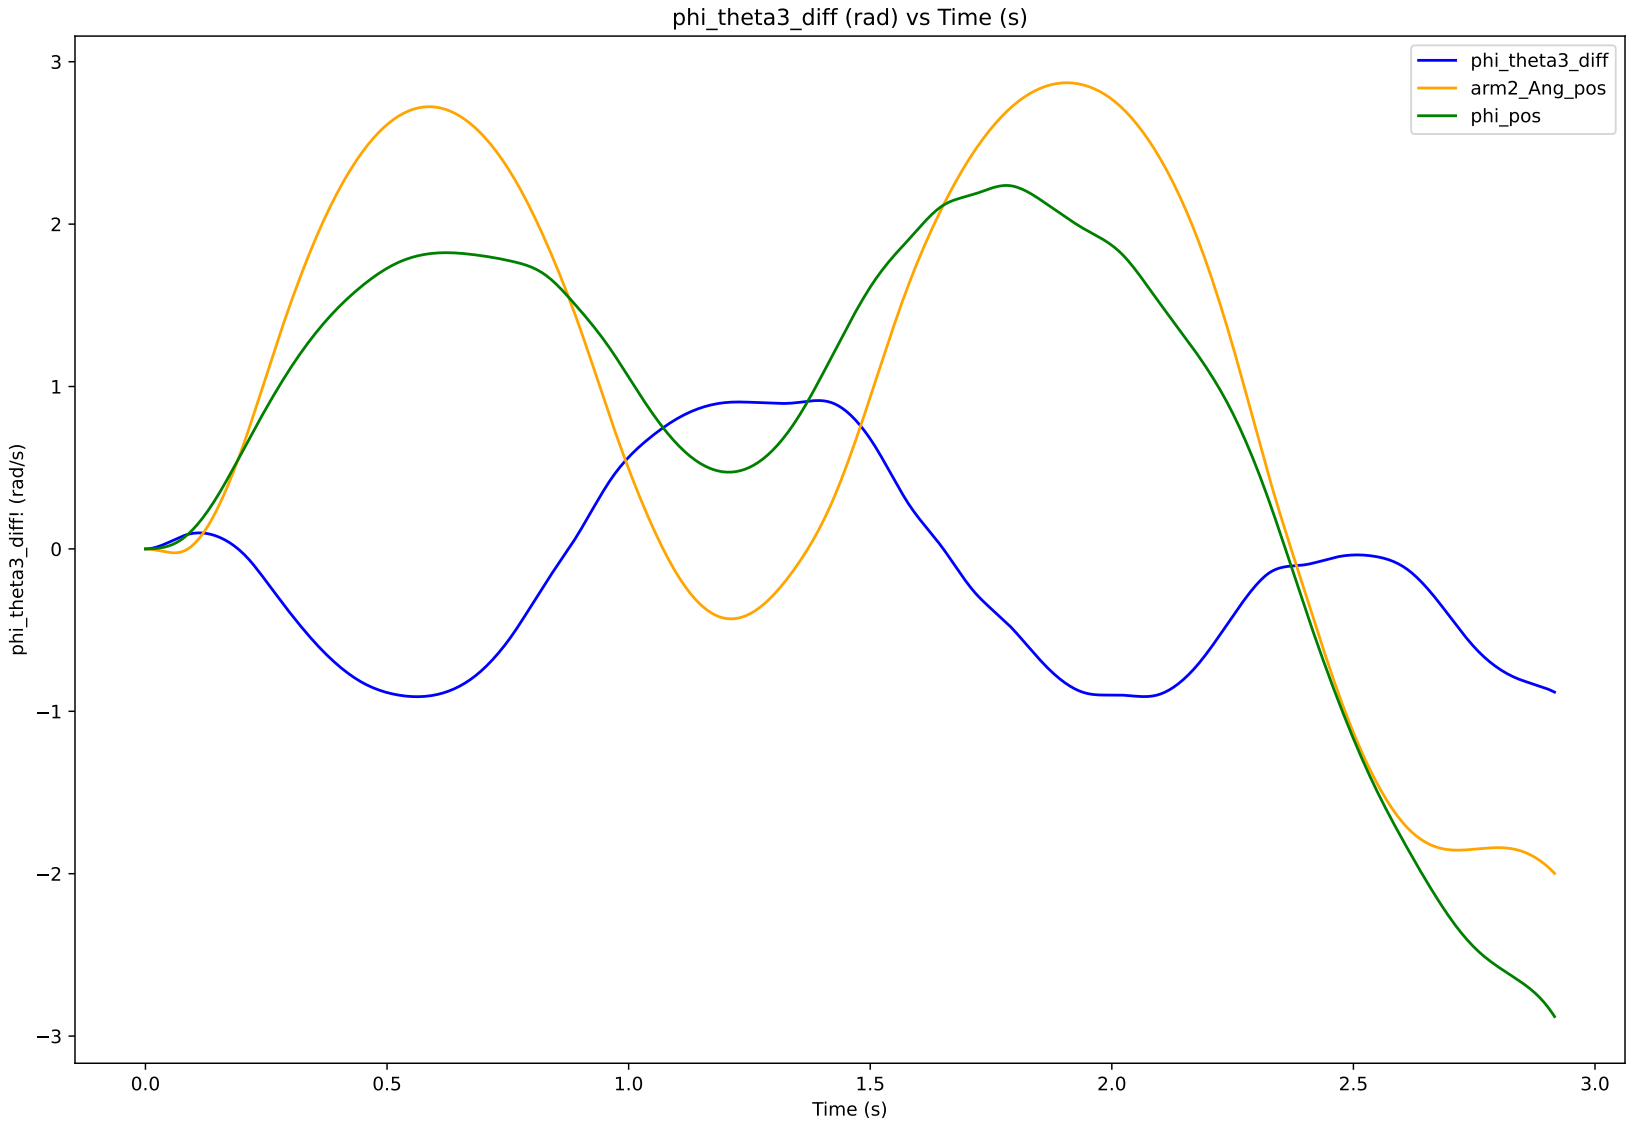
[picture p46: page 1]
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

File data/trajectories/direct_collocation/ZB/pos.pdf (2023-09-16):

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

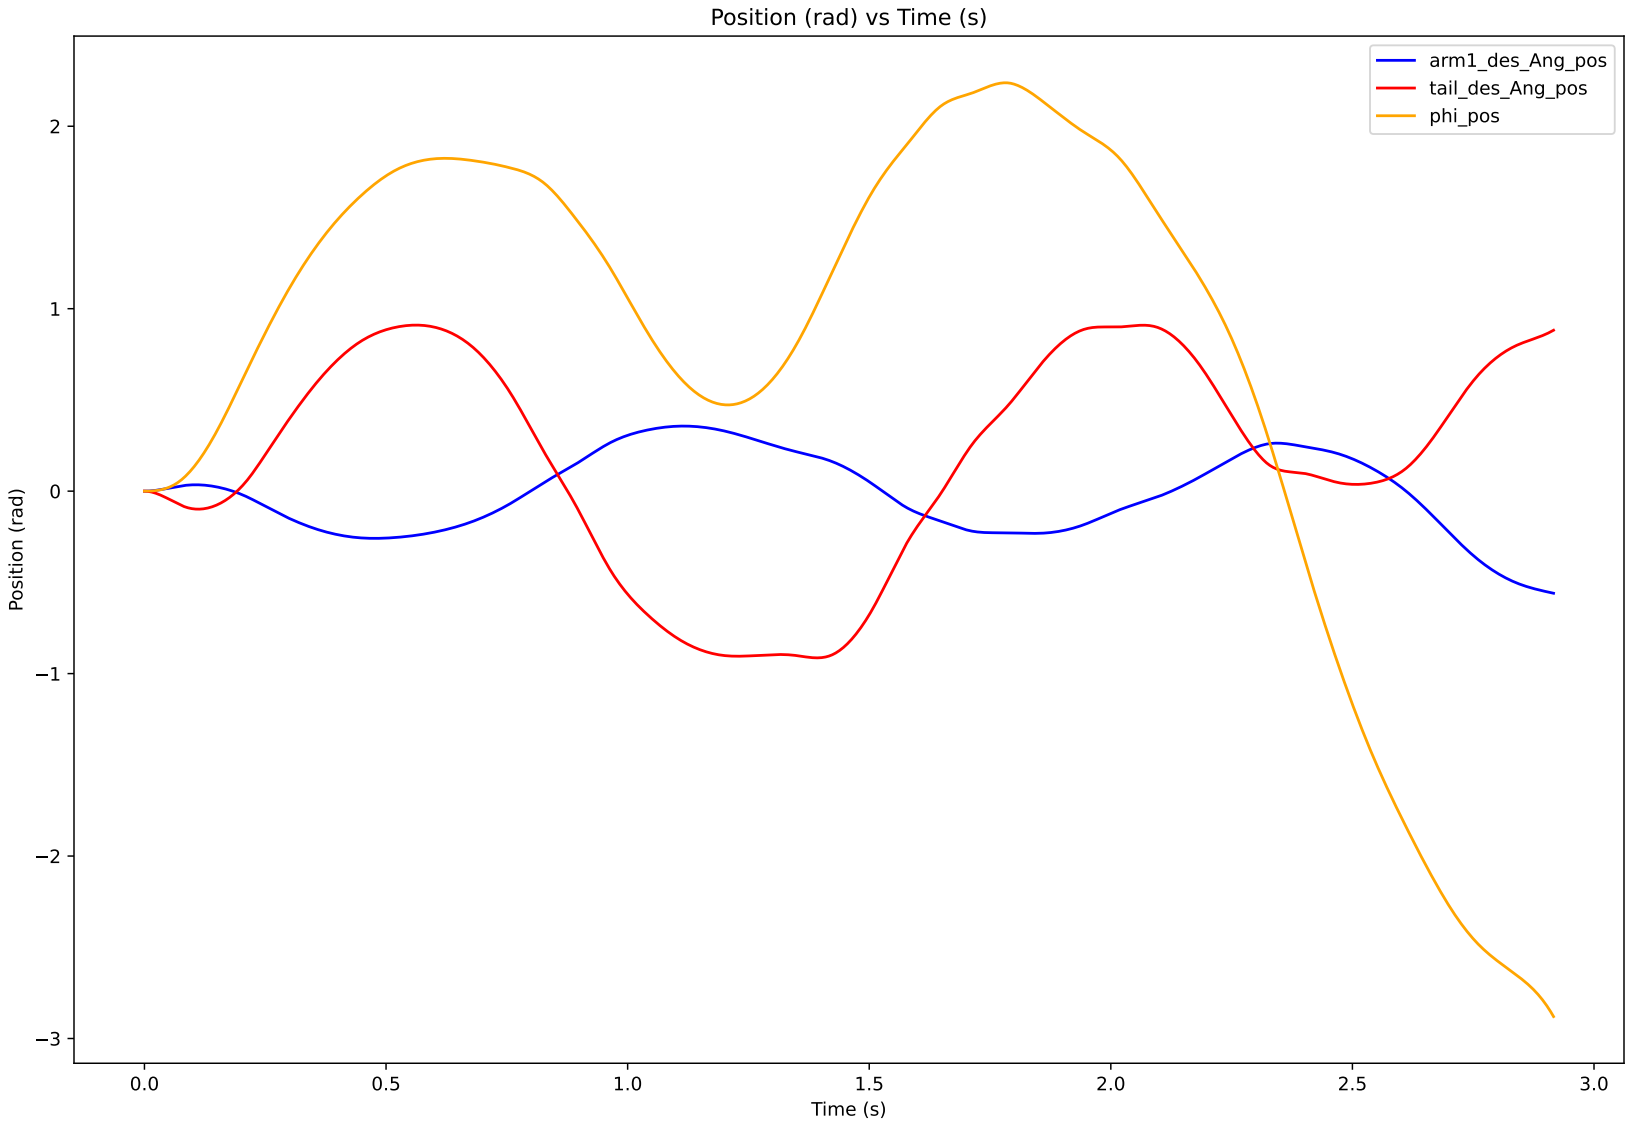
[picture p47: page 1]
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

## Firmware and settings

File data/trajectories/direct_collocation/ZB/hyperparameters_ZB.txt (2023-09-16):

n=40
tau_limit=6
initial_state=(0, 0, 0, 0, 0.0, 0)
theta_limit=[2.0943951023931953, 0.9, 2.8797932657906435]
speed_limit=12
ladder_distance=0.34
final_state=(-0.345, 0.0, 0.83, 0.75)
theta2VelMultip=1
theta3VelMultip=1
K=100
torque1_multip=1
torque2_multip=70
R=100
time_panalization=0
init_guess=[0.0, 3.0]
max_timestep=0.5
min_timestep=0.005
useRefTraj=1

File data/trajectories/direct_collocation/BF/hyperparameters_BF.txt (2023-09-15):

n=40
tau_limit=4.0
initial_state=(-0.5814944801006413, 0.5814944801006413, -2.5329708578116326, -0.633643, 0, 1.756502)
theta_limit=[2.0943951023931953, 0.9, 2.8797932657906435]
speed_limit=12
ladder_distance=0.34
final_state=(0.36, 0.03, 0.9, -1.2, 7.081415897589816, 1)
theta2VelMultip=5
theta3VelMultip=2
K=100
torque1_multip=60
torque2_multip=50
R=100
time_panalization=0
init_guess=[0.0, 4.0]
max_timestep=0.5
min_timestep=0.005

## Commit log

2023-09-15 Dump required folders
    [BF_pid.csv, BF_ref_traj (copy).csv, BF_ref_traj.csv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]
2023-09-15 Reorganised results
    [measured.csv]
2023-09-15 BOM added
2023-09-16 folder structure of reository is organized
    [BF_pid.csv, BF_ref_traj (copy).csv, BF_ref_traj.csv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]
2023-09-16 Fixed couple of errors in trajectory optimization and stabilization READMEs
2023-09-17 unnecessary files removed
    [measured.csv]
2024-04-01 landing page added
2024-04-01 landing page added in docs
2024-04-01 landing page and poster updated
